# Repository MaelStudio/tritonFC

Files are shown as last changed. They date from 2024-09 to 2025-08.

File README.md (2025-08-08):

# Triton: Water Rocket Flight Computer

I've always enjoyed launching water rockets, but I wanted to learn more about what happens during flight. That's why I built Triton, a simple flight computer based on the [XIAO ESP32S3 Sense](https://www.seeedstudio.com/XIAO-ESP32S3-Sense-p-5639.html). Featuring a BMP280 barometer and a MPU6050 IMU, Triton combines data logging to an SD card at 50 Hz, onboard video recording and even automatic parachute deployment, all in one package! This was also my first time designing a PCB so it was definitely a fun project!

<a href="https://youtu.be/Fx56_Bi1SGc" target="_blank">
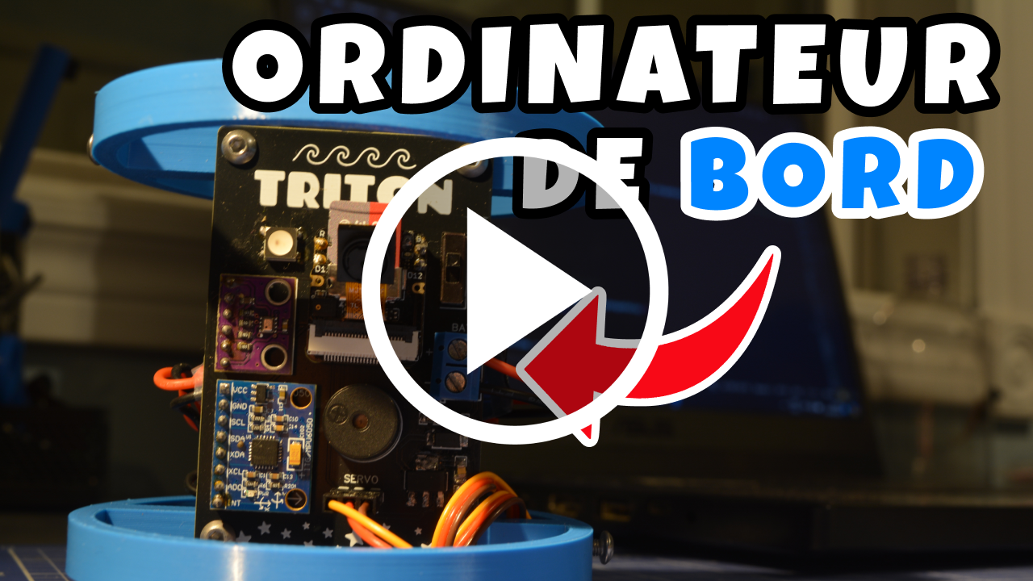
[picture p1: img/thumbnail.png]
  
</a>

## Components List

- Seeed Studio XIAO ESP32S3 Sense
- BMP280 Barometer
- MPU6050 IMU (I know, not a great pick for a rocket but at least it's dirt cheap)
- OV2640 Camera
- Passive Buzzer
- WS2812B RGB LED
- Servo Motor
- 7.4V 450 mAh Lipo Battery

## Software
Launch is detected when the acceleration hits a certain treshold. Then, Triton measures barometric altitude. When the altitude drops compared to the apogee, the parachute is deployed. It then calculates the rocket's speed to detect when the rocket has landed. Sensor data is constantly being written to the SD card at a rate of 50 Hz, in parallel with the video recording.

## SD Card

SD
Flight dir

Triton produces a flight directory on the SD card for each new flight.
Inside each flight directory, it saves:
- `flight_1.csv`: a CSV file containing flight stats
- `flight_1_logs.csv`: a CSV file containing flight data logged at ~50 Hz
- `flight_1.avi`: an AVI video file of the onboard camera footage

## Configuration file
To add more flexibility, Triton has a configuration system with different parameters that can be adjusted to achieve the desired behaviour. Triton will load the configuration from a `config.cfg` file at startup. If the file is not present, it will be created with a default configuration.
Each line of the config file must follow the following format: `parameter=value`. Comments can be added by starting a line with `#`

Here is a list of every parameter:

| Parameter | Default | Type | Description |
|---|---|---|---|
| `buzzer` | true | bool | Toggle buzzer |
| `ledBrightness` | 255 | int | LED brightness (0-255) |
| `servoHome` | 180 | int | Servo home position in degrees (0-180) |
| `servoDeploy` | 80 | int | Servo position to deploy the parachute in degrees (0-180) |
| `vidRes` | VGA | res | Video resolution, see "Onboard video" section below for resolution options |
| `vidFPS` | 20 | int | Target video fps (actual fps may vary due to ESP32S3 memory limitations) |
| `lowVoltageAlarm` | 7.40 | float  | Battery voltage threshold for alarm at startup |
| `voltageOffset` | 0.00 | float  | Offset for voltage readout |
| `launchDetectThreshold` | 1.50 | float  | Vertical acceleration (in G's) required to trigger launch detection |
| `apogeeDetectThreshold` | 1.00 | float  | Altitude difference (in meters) required to trigger apogee detection |
| `landingDetectThreshold`| 1.00 | float  | Maximum stable velocity (in m/s) allowed to consider the rocket as landed |
| `landingDetectDuration` | 3.00 | float  | Duration (in seconds) for velocity to stay below `landingDetectThreshold` to trigger landing detection |
| `landingApogeeDelay` | 5.00 | float  | Minimum delay (in seconds) between apogee detection and landing detection |
| `minDeployTime` | 2.00 | float  | Minimum parachute deployment time (in seconds) to avoid premature deployment|
| `logTemp` | /current.csv  | path | Path to the current flight log temporary file |
| `aviTemp` | /current.avi  | path | Path to the current video temporary file |
| `logDir` | /flight_%i | path | Flight directory name |
| `statsFile` | /flight_%i.csv| path | Flight statistics file name |
| `logFile` | /flight_%i_logs.csv | path | Flight logs file name |
| `aviFile` | /flight_%i.avi| path | Flight video file name |

Each file name must start with `/`, and `%i` is replaced by the flight number.

## Onboard video

Onboard video

By default the video has a VGA resolution (640x480) at 20 fps. (This GIF is compressed and is only 10 fps to reduce the file size).
The code for the video comes from the [ESP32-CAM_MJPEG2SD](https://github.com/s60sc/ESP32-CAM_MJPEG2SD) project. I only keep the necessary functions.

The resolution and fps can be modified in the configuration file. These are the options:

Frame Size | Max fps
------------ | -------------
96X96 | 45
QQVGA | 45
QCIF | 45
HQVGA | 45
240X240 | 45
QVGA | 40
CIF | 40
HVGA | 40
VGA | 20
SVGA | 20
XGA | 5
HD | 5
SXGA | 5
UXGA | 5

## Flight Data

Flight stats

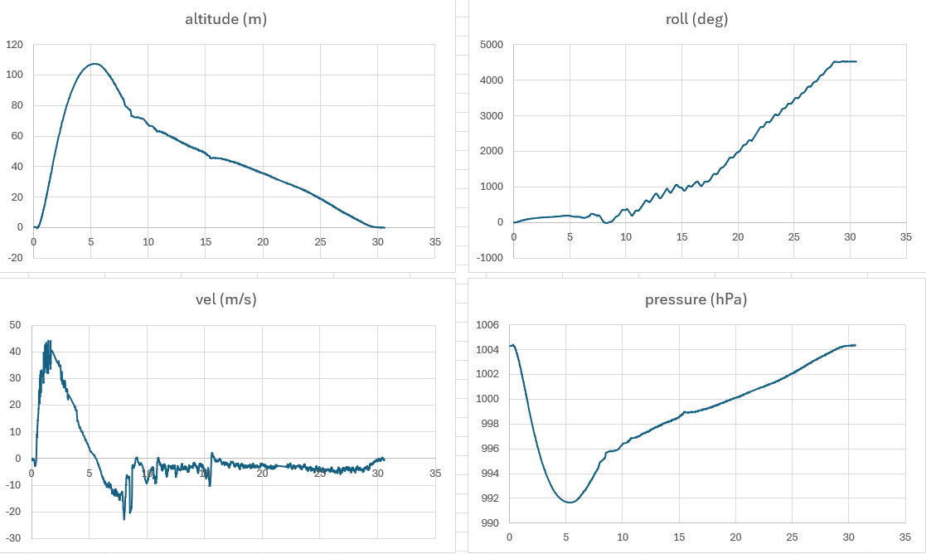
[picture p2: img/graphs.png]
Graphs


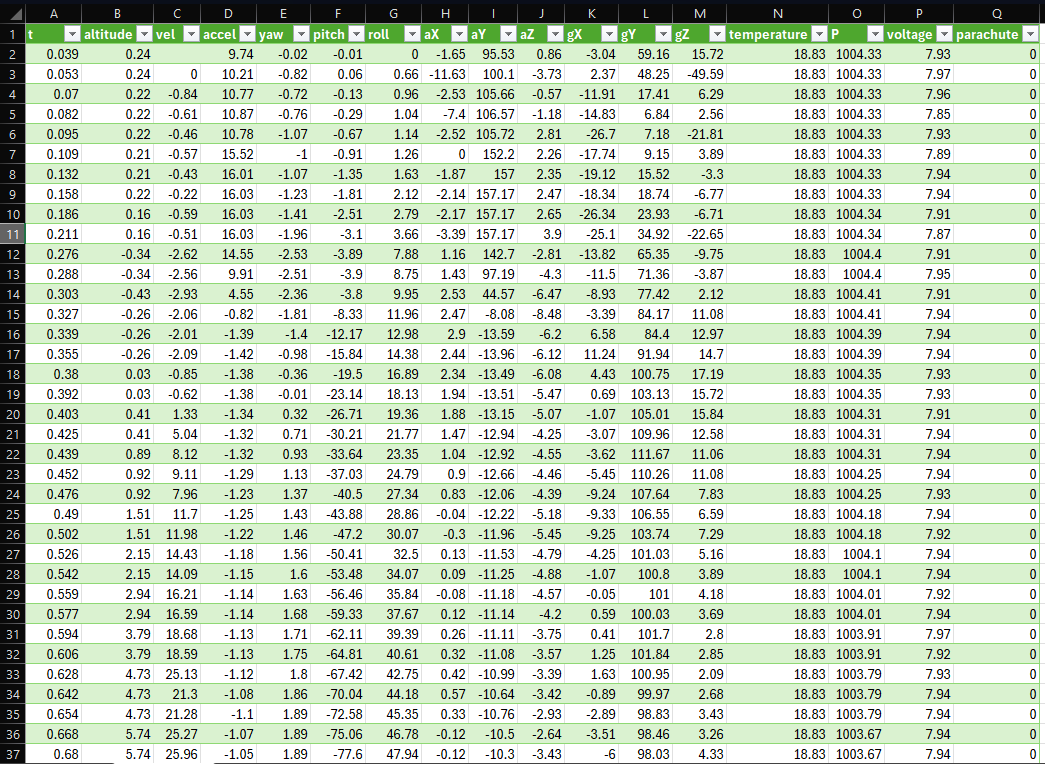
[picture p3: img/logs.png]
Logs


## Schematic

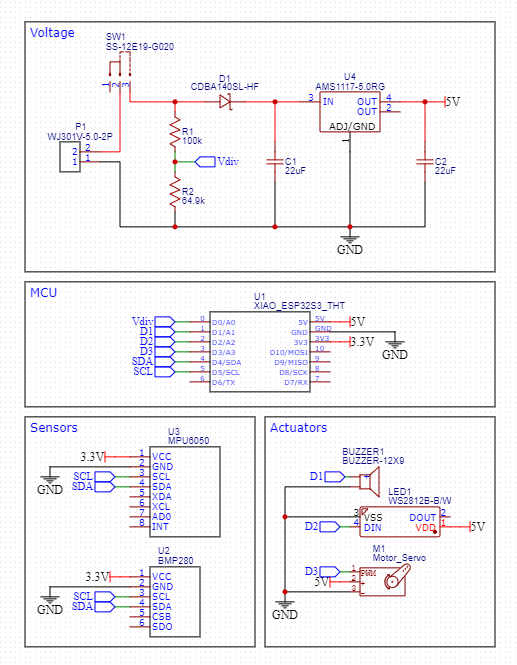
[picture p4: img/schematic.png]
Schematic


The flight computer is powered by a 2S Lipo battery (7.4V) with a capacity of 450 mAh, which is enough to keep the system running for about 2 hours. I used a linear voltage regulator to bring the battery voltage down to a stable 5V which is fed to the Xiao ESP32-S3 and the servo motor. The Xiao board integrates a 3.3V regulator.

Two resistors are wired in series to serve as a voltage divider. The values of 100k and 64.9k Ohms have been calculated so that when the battery is fully charged at 8.4V, a 3.3V signal goes to one of the ESP32's analog inputs.

I added a status LED (WS2812B), which only takes 1 digital pin, as well as a passive buzzer for additional feedback.

## PCB Design

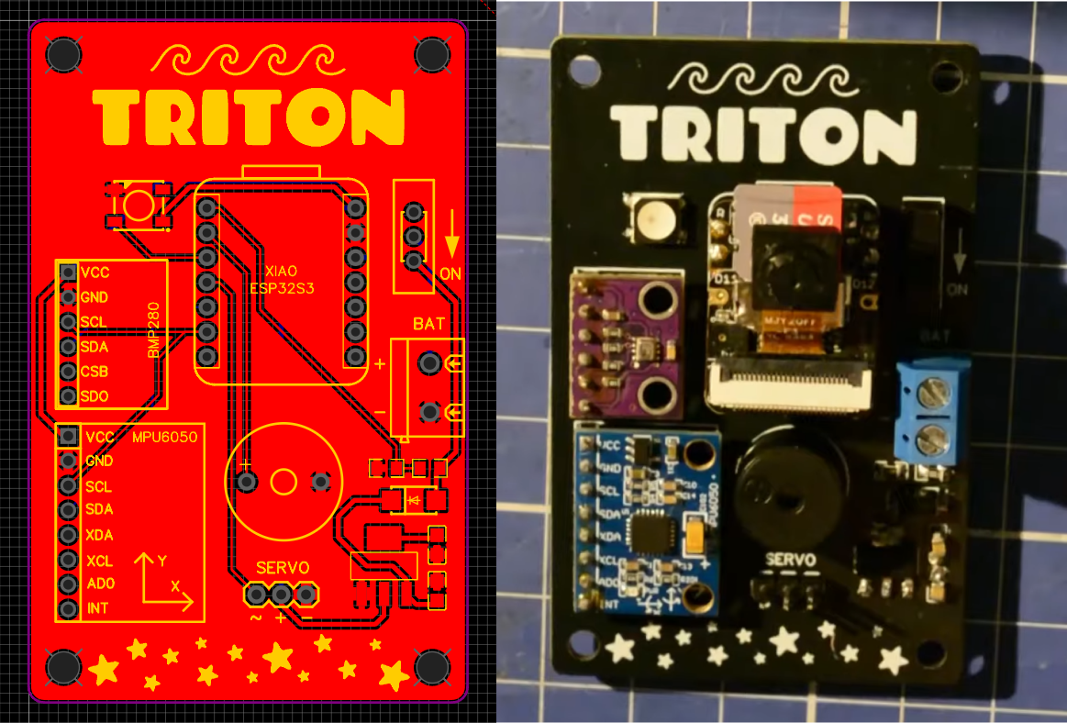
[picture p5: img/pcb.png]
PCB


## 3D Printed Brackets

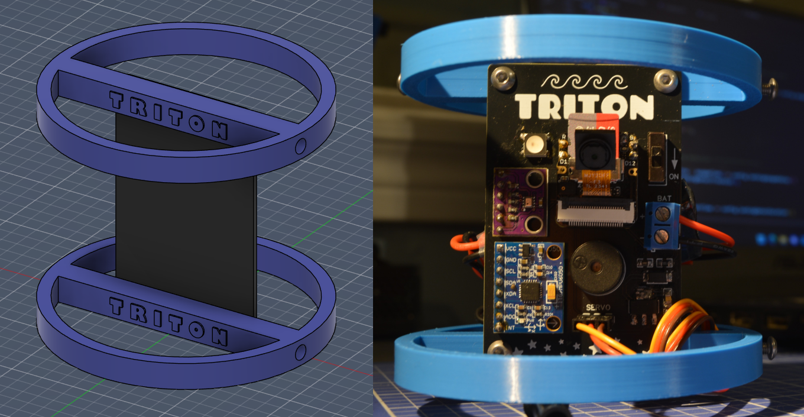
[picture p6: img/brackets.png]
Brackets


Click [here](img/brackets.stl) for the STL.

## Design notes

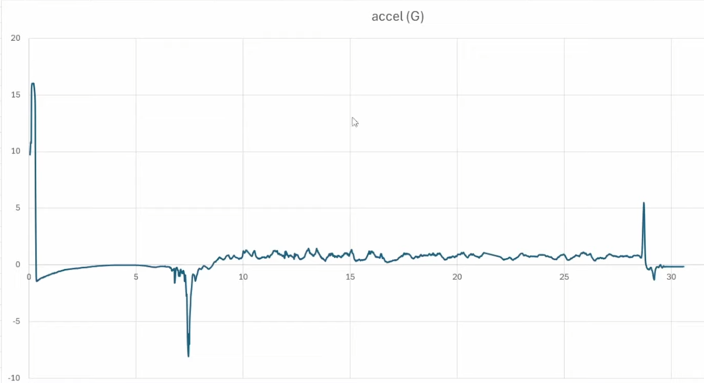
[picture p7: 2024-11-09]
img/accel.png

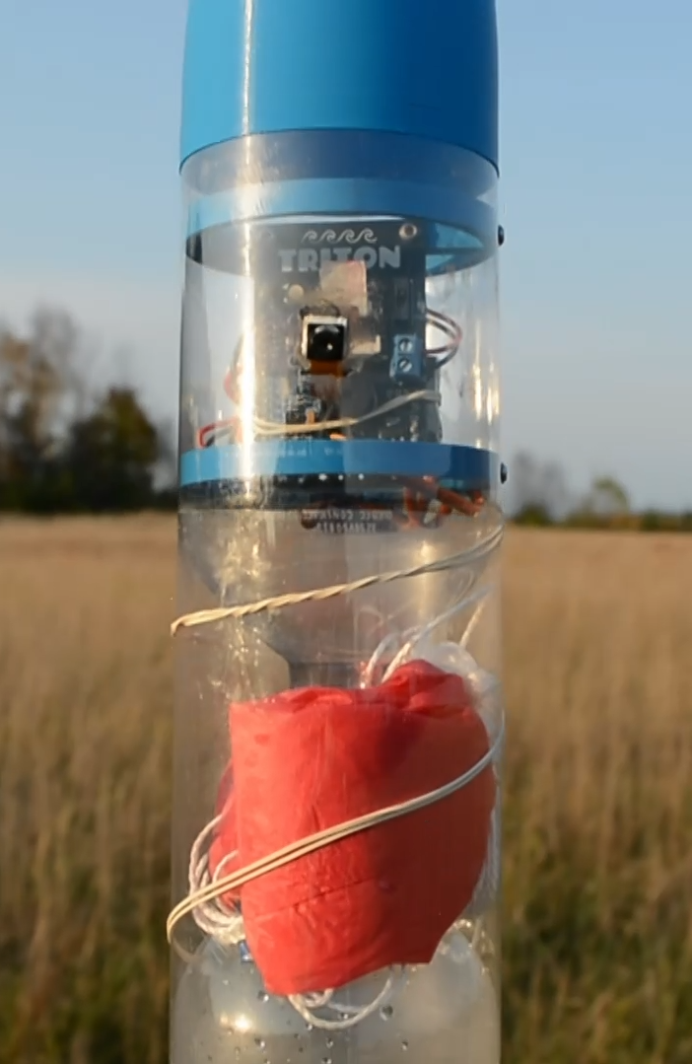
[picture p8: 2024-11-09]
img/neptune_payload.png

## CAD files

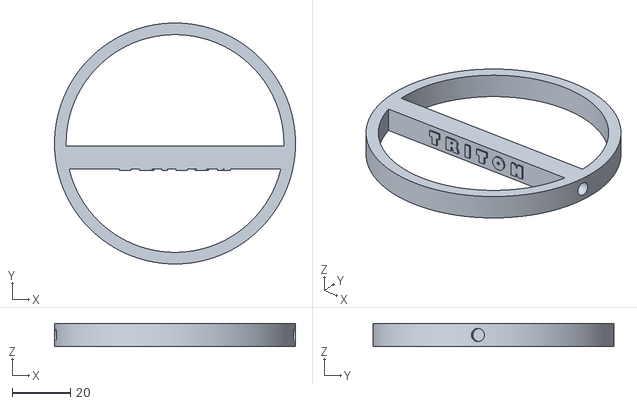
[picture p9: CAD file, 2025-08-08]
img/brackets.stl
82.5 x 82.5 x 8.00

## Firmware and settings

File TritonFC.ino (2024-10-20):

// Libraries
#include <SD_MMC.h>
#include <FS.h>
#include <Wire.h>
#include <CircularBuffer.hpp>
#include <ESP32Servo.h>
#include <Adafruit_MPU6050.h>
#include <Adafruit_BMP280.h>
#include <Adafruit_NeoPixel.h>

#include "src/mjpeg2sd/mjpeg2sd.h"

// Pins
#define BAT_PIN D0
#define BUZZER_PIN D1
#define LED_PIN D2
#define SERVO_PIN D3

// SD pins
#define SD_MMC_CLK 7
#define SD_MMC_CMD 9
#define SD_MMC_D0 8

// SD files
#define CONFIG_FILE "/config.cfg"
#define FILE_NAME_LEN 64
#define PATH_NAME_LEN (FILE_NAME_LEN + 1 + FILE_NAME_LEN) // Dir name + slash + file name

// Sensor buffers
#define SENSORS_CALIBRATION_SAMPLES 500
#define ACCEL_BUFFER_SIZE 10 // Size of the buffer used to calculate the average acceleration for launch detection
#define ALTITUDE_BUFFER_SIZE 10 // Size of the buffer used to calculate the average altitude for apogee detection
#define TIME_BUFFER_SIZE 10 // Must be <= ALTITUDE_BUFFER_SIZE. Size of the buffer used to calculate the vertical velocity based on altitude

// LED colors
#define COLOR_LOW_BAT 255, 0, 0 // Red
#define COLOR_SD 255, 255, 200 // White
#define COLOR_CAMERA 255, 40, 0 // Orange
#define COLOR_GET_FB 255, 150, 0 // Yellow
#define COLOR_IMU 0, 0, 255 // Blue
#define COLOR_BAROMETER 255, 0, 50 // Pink
#define COLOR_OK 0, 255, 0 // Green
#define COLOR_PAD_IDLE 0, 255, 0 // Green
#define COLOR_PAD_IDLE_FLASH 0, 0, 255 // Blue
#define COLOR_AIR_0 0, 0, 255 // Blue
#define COLOR_AIR_1 255, 0, 0 // Red
#define COLOR_ALTITUDE_FLASH 0, 0, 255 // Blue

// Constants
#define GRAVITY 9.80665
#define SEA_LEVEL_HPA 1005.00
#define ALPHA 0.98 // Complementary filter coefficient
#define BAT_DETECT_VOLTAGE 5.0 // Assume that the device is powered via USB if voltage is below this value (battery is unplugged)
#define BEEP_FREQ 2000 // Buzzer beep frequency, 2000 Hz is loudest

// Define config and defaults
struct Config {
  // Buzzer and LED
  bool buzzer = true; // Toggle buzzer
  byte ledBrightness = 255; // LED brightness from 0 to 255

  // Servo positions
  int servoHome = 180;
  int servoDeploy = 80;

  // Video settings
  char vidRes[10] = "VGA"; // See frameData in mjpeg2sd.h for all frame sizes
  int vidFPS = 20;

  // Battery
  float lowVoltageAlarm = 7.40; // Battery voltage is checked at startup, the alarm will ring if the voltage is below this value (On a 2S lipo, 7.4V is 3.7V per cell)
  float voltageOffset = 0.00; // Voltage readout offset

  // Launch/apogee/landing detect parameters
  float launchDetectTreshold = 1.50; // In G's, the vertical acceleration required to trigger launch detection
  float apogeeDetectTreshold = 1.00; // In meters, difference between highest recorded altitude and current altitude required to trigger apogee detection
  float landingDetectTreshold = 1.00; // In meters per second, maximum velocity allowed to consider the rocket to be stable
  float landingDetectDuration = 3.00; // In seconds, duration over which the velocity must stay below landingDetectTreshold to trigger landing detection
  float landingApogeeDelay = 5.00; // In seconds, minimum delay between apogee and landing detection
  float minDeployTime = 2.0; // In seconds, minimum time for parachute deploy
  
  char logTemp[FILE_NAME_LEN] = "/current.csv";
  char aviTemp[FILE_NAME_LEN] = "/current.avi";

  // In file names, %i will be replaced by the flight number
  char logDir[FILE_NAME_LEN] = "/flight_%i";
  char statsFile[PATH_NAME_LEN] = "/flight_%i.csv";
  char logFile[PATH_NAME_LEN] = "/flight_%i_logs.csv";
  char aviFile[PATH_NAME_LEN] = "/flight_%i.avi";
};

Config config;

// Sensors and actuators
Adafruit_MPU6050 imu;
Adafruit_BMP280 barometer;
Servo servo;
Adafruit_NeoPixel led(1, LED_PIN, NEO_GRB + NEO_KHZ800);
byte lastColor[3];

// SD
static File logFile;
char logDir[FILE_NAME_LEN];
char logFilePath[PATH_NAME_LEN];
char aviFilePath[PATH_NAME_LEN];
char statsFilePath[PATH_NAME_LEN];

// Variables

// Buffers
CircularBuffer<float, ACCEL_BUFFER_SIZE> aYBuffer; // Define circular buffer for vertical acceleration readings
CircularBuffer<float, ALTITUDE_BUFFER_SIZE> altitudeBuffer; // Define circular buffer for altitude readings
CircularBuffer<float, ALTITUDE_BUFFER_SIZE> timeBuffer;

// Sensor data
sensors_event_t accel, gyro, temp;
float yaw = 0;
float pitch = 0;
float roll = 0;
bool stable;

// State
bool launch = false;
bool apogee = false;
bool landed = false;
bool parachute = false;

// Time
float launchTime;
float apogeeTime;
float deployTime;
float flightTime;
float stableStartTime;

// Stats
int logCount = 0;
float startupVoltage;
float highestAltitude = 0;
float maxVel = 0;
float maxAccel = 0;
float deployVel;
float vidFPS;

// imu offsets
float aX_offset;
float aY_offset;
float aZ_offset;
float gX_offset;
float gY_offset;
float gZ_offset;

// altitude offset
float altitude_offset;

void setup() {
  Serial.begin(115200);
  Serial.println("\n====== Welcome to Triton FC! ======");

  pinMode(BAT_PIN, INPUT);
  pinMode(BUZZER_PIN, OUTPUT);
  led.begin();

  // Alarm if initialization fails
  if (!initAll()) {

    while (1) {
      beep(BEEP_FREQ, 120);
      ledOn();
      delay(120);
      ledOff();
      delay(50);
    }
  }
  
  // Set MPU6050 range
  imu.setAccelerometerRange(MPU6050_RANGE_16_G);
  imu.setGyroRange(MPU6050_RANGE_500_DEG);
  imu.setFilterBandwidth(MPU6050_BAND_21_HZ);

  // Set BMP280 sampling mode
  barometer.setSampling(Adafruit_BMP280::MODE_NORMAL,     /* Operating Mode. */
                  Adafruit_BMP280::SAMPLING_X2,     /* Temp. oversampling */
                  Adafruit_BMP280::SAMPLING_X16,    /* Pressure oversampling */
                  Adafruit_BMP280::FILTER_X16,      /* Filtering. */
                  Adafruit_BMP280::STANDBY_MS_1);   /* Standby time. */

  delay(200);

  // Play startup melody
  const int melody[] = {
    880, 1040, 1320, 1560
  };

  for (int i=0; i<4; i++) {
    beep(melody[i], 120);
    delay(120);
  }

  // Set servo to home orientation
  servo.attach(SERVO_PIN);
  servo.write(config.servoHome);

  Serial.println("Calibrating sensors... Stay still!");
  calibrateSensors(SENSORS_CALIBRATION_SAMPLES); // IMU and barometer calibration also acts as a delay while servo is homing

  servo.detach(); // Free up timer to prevent conflicts with tone()

  Serial.println("Setup complete");
  ledColor(COLOR_PAD_IDLE);

  // Detect launch
  while(!launch) { // While the rocket is idle on the pad, until launch is detected
    // Get time
    float now = micros() / 1000000.0;
    static float lastIdleBeep = now-1;

    // Beep and flash every second while idle
    if (now - lastIdleBeep >= 1) {
      beep(BEEP_FREQ, 60);
      ledColor(COLOR_PAD_IDLE_FLASH);
      lastIdleBeep = now;
    } else if (now - lastIdleBeep >= 0.1) {
      ledColor(COLOR_PAD_IDLE);
    }

    // Get accelerometer data
    imu.getEvent(&accel, &gyro, &temp);
    float aY = accel.acceleration.y - aY_offset; // aY = vertical acceleration
    aY /= GRAVITY; // Convert from m/s2 to G's
    aYBuffer.push(aY); // Update the circular buffer with the new aY reading

    // Calculate the average of the vertical acceleration buffer
    float sum = 0.0;
    for (int i = 0; i < ACCEL_BUFFER_SIZE; i++) {
      sum += aYBuffer[i];
    }
    float avgAY = sum / ACCEL_BUFFER_SIZE;

    if (avgAY >= config.launchDetectTreshold) {  // Compare average vertical acceleration to launchDetectTreshold
      launch = true;
      break; // Go to loop to start recording live flight data
    }
  }

  launchTime = micros() / 1000000.0; // Save launch time
  
  Serial.println("[*] Launch!");

  ledColor(COLOR_AIR_0);

  // Create CSV log file
  logFile = SD_MMC.open(config.logTemp, FILE_WRITE);
  logFile.println("t,altitude,vel,accel,yaw,pitch,roll,aX,aY,aZ,gX,gY,gZ,temperature,P,voltage,parachute"); // Write header line
  logFile.close();

  startVideo(config.aviTemp); // Create avi file and start video recording
  Serial.println("Started video recording");
}

void loop() {

  /******************** Data collection *******************/

  // Get time in seconds
  float now = (micros() / 1000000.0) - launchTime;
  static float previousTime = now;
  float dt = now - previousTime; // Get delta time
  previousTime = now;
  timeBuffer.push(now);

  // Get barometer data
  float pressure = barometer.readPressure() / 100.0;
  float altitude = barometer.readAltitude(SEA_LEVEL_HPA) - altitude_offset;
  float temperature = barometer.readTemperature();

  altitudeBuffer.push(altitude); // Update the circular buffer with the new altitude reading

  // Get accelerometer and gyroscope data
  imu.getEvent(&accel, &gyro, &temp);

  float aX = accel.acceleration.x - aX_offset;
  float aY = accel.acceleration.y - aY_offset; // aY = vertical acceleration
  float aZ = accel.acceleration.z - aZ_offset;
  float gX = gyro.gyro.x * RAD_TO_DEG - gX_offset;
  float gY = gyro.gyro.y * RAD_TO_DEG - gY_offset;
  float gZ = gyro.gyro.z * RAD_TO_DEG - gZ_offset;

  float acceleration = aY / GRAVITY; // Get acceleration in G's

  // Calculate yaw and pitch from the accelerometer data
  float accelYaw = atan2(aX, sqrt(aY*aY + aZ*aZ)) * RAD_TO_DEG;
  float accelPitch = atan2(aY, aZ) * RAD_TO_DEG;
  accelPitch -= 90; // Adjust pitch to be 0 degrees when upright

  // Integrate the gyroscope data
  yaw += gZ * dt;
  pitch += gX * dt;
  roll += gY * dt;

  // Apply complementary filter: high-pass filter for the gyroscope and a low-pass filter for the accelerometer
  yaw = ALPHA * yaw + (1.0 - ALPHA) * accelYaw;
  pitch = ALPHA * pitch + (1.0 - ALPHA) * accelPitch;
  
  float vel = (altitude - altitudeBuffer[altitudeBuffer.size() - timeBuffer.size()]) / (now - timeBuffer[0]); // Vertical velocity in m/s, calculated from previous buffered altitude readings

  // Update flight stats
  if (vel > maxVel) maxVel = vel;
  if (acceleration > maxAccel) maxAccel = acceleration;

  // Get battery voltage
  float voltage;
  if (detectBattery()) voltage = batteryVoltage();
  else voltage = 0.0;

  /******************** RGB Led *******************/

  static float ledAirColorChangeTime = now;
  static bool ledAirColor = 0;

  if (now - ledAirColorChangeTime >= 0.06) {
    if (ledAirColor) ledColor(COLOR_AIR_0);
    else ledColor(COLOR_AIR_1);
    ledAirColor = !ledAirColor;
    ledAirColorChangeTime = now;
  }

  /******************** Apogee detection & Parachute deploy *******************/

  if (!apogee) { // This runs until apogee is detected
    // Calculate the average of the altitude buffer
    float sum = 0.0;
    for (int i = 0; i < ALTITUDE_BUFFER_SIZE; i++) {
      sum += altitudeBuffer[i];
    }
    float avgAltitude = sum / ALTITUDE_BUFFER_SIZE;

    if (avgAltitude > highestAltitude) { // Keep track of highest recorded altitude
      highestAltitude = avgAltitude;
      apogeeTime = now;
    } else if (now >= config.minDeployTime && highestAltitude - avgAltitude >= config.apogeeDetectTreshold) { // Compare difference between highest recorded altitude and current altitude with apogeeDetectTreshold
      apogee = true;
      servo.attach(SERVO_PIN);
      servo.write(config.servoDeploy); // deploy parachute
      parachute = true;
      deployTime = now;
      deployVel = abs(vel);

      Serial.println("[*] Apogee!");
    }
  }

  /******************** Landing detection *******************/

  if (!landed && apogee && (now - apogeeTime) >= config.landingApogeeDelay) {
    if (abs(vel) <= config.landingDetectTreshold) {
      if (!stable) {
        stable = true;
        stableStartTime = now;
      } else if (now - stableStartTime >= config.landingDetectDuration) {
        landed = true;
        flightTime = now;

        Serial.println("[*] Landing!");

        vidFPS = stopVideo(); // close and save video file
        saveFlightData(); // save files in flight folder

        servo.detach(); // Free up timer to prevent conflicts with tone()
        while (1) {
          beepAltitude(highestAltitude); // beep out apogee
          delay(2000);
        }
      }
    } else {
      stable = false;
    }
  }

  /******************** Data logging to SD *******************/
  
  // t,altitude,vel,accel,yaw,pitch,roll,aX,aY,aZ,gX,gY,gZ,temperature,P,voltage,parachute
  logFile = SD_MMC.open(config.logTemp, FILE_APPEND);
  logFile.printf("%.3f", now);
  logFile.print(',');
  logFile.print(altitude);
  logFile.print(',');
  logFile.print(vel);
  logFile.print(',');
  logFile.print(acceleration);
  logFile.print(',');
  logFile.print(yaw);
  logFile.print(',');
  logFile.print(pitch);
  logFile.print(',');
  logFile.print(roll);
  logFile.print(',');
  logFile.print(aX);
  logFile.print(',');
  logFile.print(aY);
  logFile.print(',');
  logFile.print(aZ);
  logFile.print(',');
  logFile.print(gX);
  logFile.print(',');
  logFile.print(gY);
  logFile.print(',');
  logFile.print(gZ);
  logFile.print(',');
  logFile.print(temperature);
  logFile.print(',');
  logFile.print(pressure);
  logFile.print(',');
  logFile.print(voltage);
  logFile.print(',');
  logFile.print(parachute);
  logFile.print('\n');
  logFile.close();

  logCount++; // Keep count of the number of times new data is logged to SD card
}

bool startStorage() {
  SD_MMC.setPins(SD_MMC_CLK, SD_MMC_CMD, SD_MMC_D0);
  return SD_MMC.begin("/sdcard", true, true);
}

bool initAll() {
  ledColor(COLOR_SD);
  if (startStorage()) Serial.printf("SD card mounted. Size: %s\n", fmtSize(SD_MMC.cardSize()));
  else {
    Serial.println("[!] SD card initialization failed");
    return false;
  }

  // Load config
  if (SD_MMC.exists(CONFIG_FILE)) {
    loadConfig();
    Serial.printf("Loaded config from %s\n", CONFIG_FILE);
  } else {
    createDefaultConfig();
    Serial.printf("Created %s to store default config\n", CONFIG_FILE);
  }
  
  led.setBrightness(config.ledBrightness);

  ledColor(COLOR_LOW_BAT);
  if (detectBattery()) {
    startupVoltage = batteryVoltage();
    if (startupVoltage > config.lowVoltageAlarm) Serial.printf("Battery is at %.2fV\n", startupVoltage);
    else {
      Serial.printf("[!] Low battery: %.2fV\n", startupVoltage);
      return false;
    }
  } else {
    Serial.println("No battery detected");
    startupVoltage = 0.0;
  }
  
  ledColor(COLOR_CAMERA);
  if (startCam(config.vidRes)) Serial.println("Camera initialized");
  else {
    Serial.println("[!] Camera init failed");
    return false;
  }

  ledColor(COLOR_GET_FB);
  if (prepRecording(config.vidFPS)) Serial.println("Ready to record");
  else {
    Serial.println("[!] Failed to get camera frame");
    return false;
  }

  ledColor(COLOR_IMU);
  if (imu.begin()) Serial.println("MPU6050 initialized");
  else {
    Serial.println("[!] MPU6050 init failed");
    return false;
  }

  ledColor(COLOR_BAROMETER);
  if (barometer.begin(0x76)) Serial.println("BMP280 initialized");
  else {
    Serial.println("[!] BMP280 init failed");
    return false;
  }

  ledColor(COLOR_OK);
  return true;
}

void createDefaultConfig() {
  File configFile = SD_MMC.open(CONFIG_FILE, FILE_WRITE);

  configFile.print("buzzer=");
  configFile.println(config.buzzer ? "true" : "false");
  configFile.print("ledBrightness=");
  configFile.println(config.ledBrightness);
  configFile.print("servoHome=");
  configFile.println(config.servoHome);
  configFile.print("servoDeploy=");
  configFile.println(config.servoDeploy);
  configFile.print("vidRes=");
  configFile.println(config.vidRes);
  configFile.print("vidFPS=");
  configFile.println(config.vidFPS);
  configFile.print("lowVoltageAlarm=");
  configFile.println(config.lowVoltageAlarm);
  configFile.print("voltageOffset=");
  configFile.println(config.voltageOffset);
  configFile.print("launchDetectTreshold=");
  configFile.println(config.launchDetectTreshold);
  configFile.print("apogeeDetectTreshold=");
  configFile.println(config.apogeeDetectTreshold);
  configFile.print("landingDetectTreshold=");
  configFile.println(config.landingDetectTreshold);
  configFile.print("landingDetectDuration=");
  configFile.println(config.landingDetectDuration);
  configFile.print("landingApogeeDelay=");
  configFile.println(config.landingApogeeDelay);
  configFile.print("minDeployTime=");
  configFile.println(config.minDeployTime);
  configFile.print("logTemp=");
  configFile.println(config.logTemp);
  configFile.print("aviTemp=");
  configFile.println(config.aviTemp);
  configFile.print("logDir=");
  configFile.println(config.logDir);
  configFile.print("statsFile=");
  configFile.println(config.statsFile);
  configFile.print("logFile=");
  configFile.println(config.logFile);
  configFile.print("aviFile=");
  configFile.println(config.aviFile);

  configFile.close();
}

void loadConfig() {
  File configFile = SD_MMC.open(CONFIG_FILE);

  while (configFile.available()) {
    String line = configFile.readStringUntil('\n');
    line.trim(); // Remove leading and trailing whitespace

    // Skip empty lines or comments
    if (line.length() == 0 || line.startsWith("#")) {
      continue;
    }

    int delimiterIndex = line.indexOf('=');
    if (delimiterIndex == -1) continue;

    String key = line.substring(0, delimiterIndex);
    String value = line.substring(delimiterIndex + 1);
    key.trim();
    value.trim();

    // Update the Config struct based on key-value pairs
    if (key == "buzzer") {
      config.buzzer = (value.equalsIgnoreCase("true")) ? true : false;
    } else if (key == "ledBrightness") {
      if (value.toInt() > 255) {
        config.ledBrightness = 255;
      } else {
        config.ledBrightness = (byte)value.toInt();
      }
    } else if (key == "servoHome") {
      config.servoHome = value.toInt();
    } else if (key == "servoDeploy") {
      config.servoDeploy = value.toInt();
    } else if (key == "vidRes") {
      value.toCharArray(config.vidRes, sizeof(config.vidRes));
    } else if (key == "vidFPS") {
      config.vidFPS = value.toInt();
    } else if (key == "lowVoltageAlarm") {
      config.lowVoltageAlarm = value.toFloat();
    } else if (key == "voltageOffset") {
      config.voltageOffset = value.toFloat();
    } else if (key == "launchDetectTreshold") {
      config.launchDetectTreshold = value.toFloat();
    } else if (key == "apogeeDetectTreshold") {
      config.apogeeDetectTreshold = value.toFloat();
    } else if (key == "landingDetectTreshold") {
      config.landingDetectTreshold = value.toFloat();
    } else if (key == "landingDetectDuration") {
      config.landingDetectDuration = value.toFloat();
    } else if (key == "landingApogeeDelay") {
      config.landingApogeeDelay = value.toFloat();
    } else if (key == "minDeployTime") {
      config.minDeployTime = value.toFloat();
    } else if (key == "logTemp") {
      value.toCharArray(config.logTemp, sizeof(config.logTemp));
    } else if (key == "aviTemp") {
      value.toCharArray(config.aviTemp, sizeof(config.aviTemp));
    } else if (key == "logDir") {
      value.toCharArray(config.logDir, sizeof(config.logDir));
    } else if (key == "statsFile") {
      value.toCharArray(config.statsFile, sizeof(config.statsFile));
    } else if (key == "logFile") {
      value.toCharArray(config.logFile, sizeof(config.logFile));
    } else if (key == "aviFile") {
      value.toCharArray(config.aviFile, sizeof(config.aviFile));
    } else {
      Serial.printf("Unknown config key: %s\n", key);
    }
  }
}

// IMU and barometer calibration
// Barometer calibration sets ground altitude
void calibrateSensors(int samples) {
  aX_offset = 0;
  aY_offset = 0;
  aZ_offset = 0;
  gX_offset = 0;
  gY_offset = 0;
  gZ_offset = 0;
  altitude_offset = 0;

  for (int i=0; i<samples; i++) {
    imu.getEvent(&accel, &gyro, &temp);
    aX_offset += accel.acceleration.x;
    aY_offset += accel.acceleration.y;
    aZ_offset += accel.acceleration.z;
    gX_offset += gyro.gyro.x * RAD_TO_DEG;
    gY_offset += gyro.gyro.y * RAD_TO_DEG;
    gZ_offset += gyro.gyro.z * RAD_TO_DEG;
    altitude_offset += barometer.readAltitude(SEA_LEVEL_HPA);
    delay(1);
  }

  // Calculate averages
  aX_offset /= samples;
  aY_offset /= samples; aY_offset -= GRAVITY; // Gravity compensation for Y-axis
  aZ_offset /= samples;
  gX_offset /= samples;
  gY_offset /= samples;
  gZ_offset /= samples;
  altitude_offset /= samples;

  Serial.printf("IMU calibrated with offsets: %.6f %.6f %.6f %.6f %.6f %.6f\n", aX_offset, aY_offset, aZ_offset, gX_offset, gY_offset, gZ_offset);
}
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

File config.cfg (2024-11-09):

buzzer=true
ledBrightness=255

servoHome=180
servoDeploy=80

vidRes=VGA
vidFPS=20

lowVoltageAlarm=7.40
voltageOffset=0.05

launchDetectTreshold=1.50
apogeeDetectTreshold=1.00
landingDetectTreshold=1.00
landingDetectDuration=3.00
landingApogeeDelay=5.00
minDeployTime=2.00

logTemp=/current.csv
aviTemp=/current.avi
logDir=/flight_%i
statsFile=/flight_%i.csv
logFile=/flight_%i_logs.csv
aviFile=/flight_%i.avi

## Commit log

2023-12-18 Remove unused stuff
    [configs.txt]
2024-01-05 Revert "new"
    This reverts commit 41d865431e235197a51c6ee81b65dc09d640a552.
    [mjpeg2sd.cpp]
2024-01-05 Revert "Remove unused stuff"
    This reverts commit 5f4924cef35d97adada22e80ae4766b7f3347918.
    [configs.txt]
2024-01-05 Remove non-arduino files
    [configs.txt]
2024-01-05 Cam board
2024-06-24 Fix frame timer
2024-06-24 Revert "Remove mic"
    This reverts commit b93234492fb7780fdcaa283c0da067345f2c091f.
    [mjpeg2sd.cpp]
2024-06-24 Reapply "Remove mic"
    This reverts commit 42a3c066db2dfb9e2a3ad549a6b6aeeacba4f989.
    [mjpeg2sd.cpp]
2024-06-24 Remove log and cleanup code
    Every LOG function has been replaced by Serial prints
    [mjpeg2sd.cpp]
2024-06-24 Print new lines
2024-06-25 Remove Arduino import
2024-07-02 Read IMU and barometer data
2024-07-03 Launch detect switch
2024-07-04 Servo motor
2024-07-04 Add back init prints
2024-07-10 Detach servo to prevent conflicts with tone()
    [TritonFC.ino]
2024-07-19 IMU calibration and angle calculations
2024-07-23 Remove max video frames
2024-07-31 Detect landing
2024-08-04 Replace "apogee" by "parachute" in log file
    [TritonFC.ino]
2024-08-06 RGB led
2024-08-07 Flash RGB Led while in the air
2024-08-07 Read battery voltage
2024-08-07 Remove unused frameStruct data
2024-08-19 buzzer toggle in config
    [TritonFC.ino]
2024-08-19 Servo positions in config
2024-08-19 ledBrightness and lowVoltageAlarm in config
2024-08-19 Change servo pos
2024-08-22 Add voltage read offset
2024-08-26 Adjust voltage read coefficient
2024-08-26 Remove "..." prints while recording
2024-09-18 Import schematic
2024-09-18 Add pcb image
2024-09-18 Reduce pcb image size
2024-09-18 Revert "Reduce pcb image size"
    This reverts commit 4350fdada39ae851566ce4ffe9fb260d45bce273.
2024-09-19 Change pcb.png
2024-09-19 Add brackets.png
2024-10-20 Change landingDetect defaults
2024-11-09 Add config.cfg file
    [config.cfg]
2024-11-14 Add gerber
2025-08-08 Add STL
    [brackets.stl]
